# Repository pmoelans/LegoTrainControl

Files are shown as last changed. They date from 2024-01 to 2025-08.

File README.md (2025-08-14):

# Introduction
This project started out as a hobby project and got a tiny bit out of hand. The goal of the project was to create a custom controller for lego power functions trains. 
The specific goal was to get rid of the infrared controller and use Wifi instead. The Wifi turned out to be an issue since the connection time of the arduino boards with wifi can take a while and the attention span of 
kids is rather limited. Hence the current controller is now working with the ESPNOW protocol. 
Currently the project contains 3 seperate modules:
+ The train controller
+ The switch controller
+ The user controller(UI)
The following paragraphs describe the seperate modules.

## The train controller
The train controller is the hardware and software that is onboard the train itself and it controls the power functions motor. This module is build around the QTPY-C3 ESP32 platform. 
The form factor was the driving force behind the choice of platform. Namely the entire contraption (including battery) needs to have a similar size as the battery box of a powerfunctions motor. This puts some
serious constraints on the design. The platform also needs a few additional features with respect to the original power functions versions:
+ An emergency stop function: once this command is given, all trains need to stop as quickly as possible. This is a software thing and does not impact the overal design
+ An shutdown feature: once this command is given. The train stops and the entire circuit needs to be shut down. This has an impact on the hardware of the project in such a way that the ESP can shut itself down.
+ The basic idea for this controller was first found on https://mattzobricks.com/. A must see for Lego train enthousiasts. On this site there was a section where a similar controller as mine was created. This controller
  did not fit my exact needs since it was used together with the Rocrail platform. But it served as a firm basis for the controller described here.
 
 ### Hardware
 The board is build up around the following two modules:
 + QTPY-C3 ESP32
 + TB6612 Dual motor driver (TB6612FNG). Instead of just using the chip, I used the existing ready made breakout board
 + Custom build PCB(I'm not an electronics engineer so I'm sure that things could have been done better and more efficiently)
 + 3D printed casing in which you can snap in the PCB board as well as fit the lego power functions connectors. The shape of the box is heavily inspired on the original power functions box and the box on https://mattzobricks.com/.
  
## The swith controller
The switch controller is the hard and software that is used to control the switch. We use end switches in order to detect whether the switch is in its final position. This works a bit easer since each type of lego
switch has its own movement which might take a little more time to make the actual switch.

### Hardware
Main parts:
+ ATTiny85A
+ L9110 motor controller
+ Small lego engine
+ Two end switches
+ Custom PCB
+ 3D printed casing for the PCB.

## The user controller(UI)
This is the handheld controller that is used to control the trains(for now). We can control the switches as well, but the UI is specifically designed to quickly change between trains in question. You can have multple trains
that are connected to the controller. The only limit is the memory of the ESP32.

### Hardware
The design of the UI is pretty straight forward and contains of:
+ A rotary button:
  + Rotating the button speeds up or slows down the train
  + Pushing the rotary button switches to the next train that is registered.
+ Two buttons:
  + Emergency stop button: stops all trains
  + A shut down button: shuts down all trains
This controller is also build around the QTPY-C3 board. 
  
### Software
The software uses the ESPNOW protocol the communicate with all the trains. The controller has two functions:
+ Listens for new trains: Upon startup of a train (battery is on) it will start sending connection requests to the controller. This is done every few seconds until the controller sends an accept message to the train.
  After this accept request the train will send its status every 10s to the controller. The trains need to be identified and the unique identifier used is the mac-address of the ESP32.
  This mac-address together with the current state of the train(e.g. speed, battery voltage) are kept as well.
+ Controls the current train: Every time the rotary button is used, a message is send that reflects the changes. This message is only send to the train that is active at the moment. The state of the current train is also updated once the
    rotary button is used. Every new train creates a new entry in the dictionary
If one of the two other buttons is pressed, the message is send to all the trains.

# Future work

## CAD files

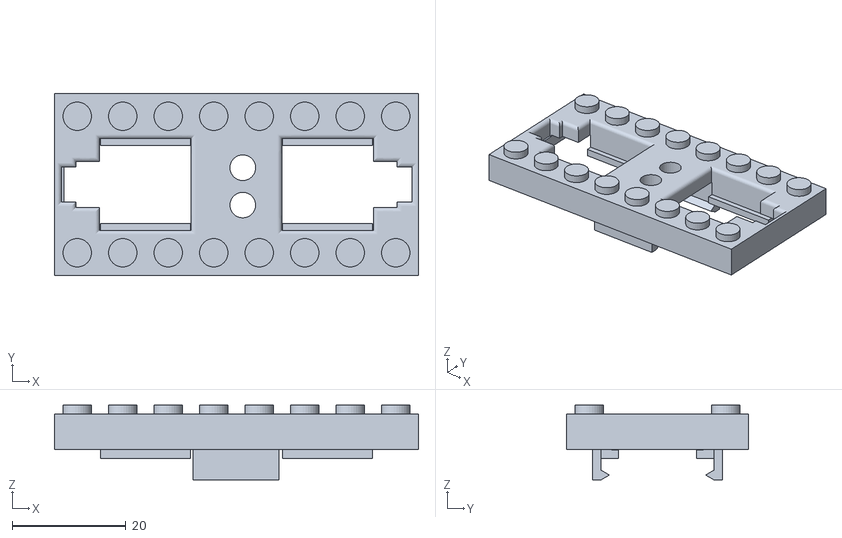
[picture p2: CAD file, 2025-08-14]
LegoEngineControlESPNow/Stl/TopSnap.stl
64.0 x 32.0 x 13.2

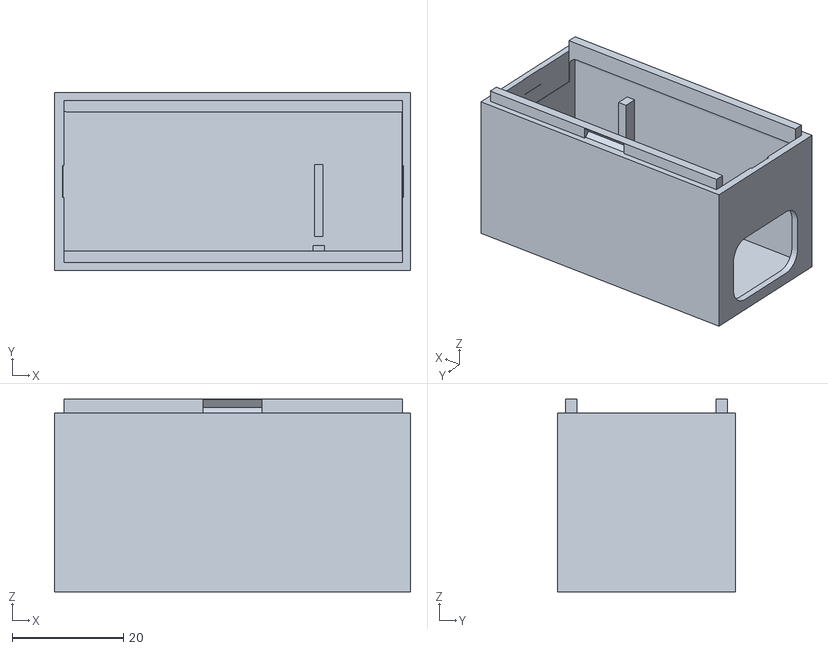
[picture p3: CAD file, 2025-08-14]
LegoEngineControlESPNow/Stl/Bottom.stl
64.0 x 32.0 x 34.7

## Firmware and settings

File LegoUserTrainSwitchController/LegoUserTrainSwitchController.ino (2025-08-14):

#include "RotaryBtn.h"
#include "Settings.h"
#include <esp_now.h>
#include <WiFi.h>
#include <esp_wifi.h>
#include <ArduinoJson.h>
#include "ClientHandler.h"
#include <Arduino_Helpers.h>
#include <AH/Hardware/Button.hpp>
#include <SoftwareSerial.h>
#include "enums.h"

#define DEBUG true // Set to false to disable debug prints
#if DEBUG
#define debug(x) Serial.print(x)
#define debugln(x) Serial.println(x)
#else
#define debug(x)
#define debugln(x)
#endif

int counter = 0;
int resendCount = 0;
int maxResendCount = 10;
int restartCount=0;
bool preState=1;
uint8_t ownMac[] = {0xC0, 0x4E, 0x30, 0x80, 0x72, 0x4C};

ClientHandler clientHandler;
SoftwareSerial mySerialLink(Rx, Tx);  //16 MOSI(RX) 14 MISO(TX)   

RotaryBtn SpeedBtn(5, 6, 1);
RotaryBtn SwitchBtn(7,8,11);

bool trainSelected = false;
bool reverseDirection = false;
long debounceDelta = 1000;
long pressTime =millis();

esp_now_peer_info_t peerInfo;
const int freq = 5000;//30000;
const int motorchannel1 = 0;
const int resolution = 8;
bool SwitchLights = false;


// callback function that will be executed when data is received
void OnDataRecv(const uint8_t* mac_addr, const uint8_t* incomingData, int len) {

  debug("Packet received from: ");
  String clientId =  PrintMac(mac_addr);

  Serial.print("clientId:");
  Serial.println(clientId);

  //deserialize the data:
  //=====================
  DynamicJsonDocument doc(256);
  deserializeJson(doc, incomingData);

  //Write the incoming message to the serial connection
  //===================================================
  //char* Mymessage= (char*) incomingData; 
  //mySerialLink.write(Mymessage);

  String clientType= doc["ClientType"];



  //check if we need to add the client:
  //===================================
  if (clientHandler.CheckClient(clientId, (uint8_t*)mac_addr,clientType)) {
    //register the peer device:
    //=========================
    //debug("Registering new client: ");
    //debugln((uint8_t*)mac_addr);
    memcpy(peerInfo.peer_addr, mac_addr, 6);
    peerInfo.channel = 0;
    peerInfo.encrypt = false;
    //Serial.println(peerInfo.peer_addr);
    // Add peer
    if (esp_now_add_peer(&peerInfo) != ESP_OK) {
      debugln("Failed to add peer");
      return;
    }
  }
  else
  {
    debug("I know this client already: ");
    debugln(clientId);
  }
}

void IncreaseSpeedCallBack()
{
  debugln("Increase Speed");
  clientHandler.clientList[clientHandler.CurrentTrainId].UpdateState(10);
  SendMessage(clientHandler.clientList[clientHandler.CurrentTrainId].Idx);
}
void DecreaseSpeedCallBack()
{
  debugln("Decrease Speed");
  clientHandler.clientList[clientHandler.CurrentTrainId].UpdateState(-10);
  SendMessage(clientHandler.clientList[clientHandler.CurrentTrainId].Idx);
}
void UpdateSwitchStateCallback()
{
  debugln("Engage Switch");
  clientHandler.clientList[clientHandler.CurrentSwitchId].UpdateState(1);
  SendMessage(clientHandler.clientList[clientHandler.CurrentSwitchId].Idx); 
}
void NextTrainClient()
{
  debugln("Fetch next train");
  //deactivate blinking on current train
  clientHandler.clientList[clientHandler.CurrentTrainId].DeactivateBlink();
  SendMessage(clientHandler.clientList[clientHandler.CurrentTrainId].Idx);
  clientHandler.GoToNextClient(1,"Train");
  clientHandler.clientList[clientHandler.CurrentTrainId].ActivateBlink();
  SendMessage(clientHandler.clientList[clientHandler.CurrentTrainId].Idx);
}
void NextSwitchClient()
{
  debugln("Fetch next switch");
  clientHandler.GoToNextClient(1,"Switch");
}
void PreviousSwitchClient()
{
  debugln("Fetch previous switch");
  clientHandler.GoToNextClient(-1,"Switch"); 
}
void setup() {

  if(DEBUG)
  {
    Serial.begin(115200);
  }

  InitButtons();

  //Set device as a Wi-Fi Station
  WiFi.mode(WIFI_STA);
  esp_wifi_set_mac(WIFI_IF_STA, ownMac);
  mySerialLink.begin(115200);
  //Init ESP-NOW && restart the esp if it does not work
  while ((esp_now_init() != ESP_OK) && (restartCount<maxRetryCountEspNowStart)) {
    debugln("Error initializing ESP-NOW");
    restartCount+=1;
    delay(100);
  }
  if(restartCount==maxRetryCountEspNowStart)
  {
    ESP.restart();
  }

  debugln("EspNow started");

  // Once ESPNow is successfully Init, we will register for recv CB to
  // get recv packer info
  esp_now_register_recv_cb(OnDataRecv);

  //Register the funtions:
  SpeedBtn.RegisterCallBack(Motion::Positive,IncreaseSpeedCallBack);
  SpeedBtn.RegisterCallBack(Motion::Negative, DecreaseSpeedCallBack);
  SpeedBtn.RegisterCallBack(Motion::BtnPress,NextTrainClient);

  SwitchBtn.RegisterCallBack(Motion::Positive, NextSwitchClient);
  SwitchBtn.RegisterCallBack(Motion::Negative, PreviousSwitchClient);
  SwitchBtn.RegisterCallBack(Motion::Negative, UpdateSwitchStateCallback);

  ledcSetup(motorchannel1,freq,resolution); 
  ledcAttachPin(Led,motorchannel1);
  ledcWrite(motorchannel1, 180);
}


void InitButtons() {
  pinMode(buttonEBreak, INPUT);
  pinMode(buttonShutDown, INPUT);
  pinMode(switchLights,INPUT);

  pinMode(nextTrainBtn,INPUT);
  pinMode(PowerHold, OUTPUT);

  //pinMode(Led,OUTPUT);
  digitalWrite(PowerHold,HIGH);

  //digitalWrite(Led,HIGH);
}
void Blink(int cnt) {

  //for (int i = 0; i < cnt; i++) {
  //  digitalWrite(Led, LOW);
  //  delay(50);
  //  digitalWrite(Led, HIGH);
  //  delay(50);
  //}
}

void CheckReverseBtn(Button btn) {
  if (btn.update() == Button::Falling) {
    clientHandler.clientList[clientHandler.CurrentTrainId].ReverseDirection();
    return;
  }
}
//Shut yourself down please:
void ShutDown()
{
  digitalWrite(PowerHold,LOW);
}
void CheckLightsBtn()
{
  if(digitalRead(switchLights)==HIGH)
  {
    SwitchLights=true;
    SendMessage(clientHandler.clientList[clientHandler.CurrentTrainId].Idx);
  }
}
void CheckShutDownStateBtn() 
{
  if (digitalRead(buttonShutDown) == HIGH) {
    //Go over all the clients and perform a shutDown
    for(int i=0;i<clientHandler.idx;i++)
    {
      clientHandler.clientList[i].EnableShutDown();
      SendMessage(i);     
    }   

    delay(100);
    ShutDown(); 
  }
}

void CheckEmergencyBrakeStateBtn() {
  if (digitalRead(buttonEBreak) == HIGH) {
     for(int i=0;i<clientHandler.idx;i++)
    {
      clientHandler.clientList[i].EnableEmergencyBrake();
      SendMessage(i);     
      clientHandler.clientList[clientHandler.CurrentTrainId].DisableEnableEmergencyBrake();
    }       
  }
}

void loop() {
  CheckShutDownStateBtn();
  CheckEmergencyBrakeStateBtn();
  //GetNextClient();
  
  SpeedBtn.CheckState();
  SwitchBtn.CheckState();  
}

void SendMessage(int index)
{
  debug(clientHandler.clientList[index].ClientId);
  PrintMac(clientHandler.clientList[index].MacAddress);
  String msg = clientHandler.clientList[index].CreateJson();
 
  char Msg[90];
  StaticJsonDocument<90> statusDoc;
  statusDoc["ClientId"] = clientHandler.clientList[index].ClientId;
  statusDoc["Power"] = clientHandler.clientList[index].State;
  statusDoc["ShutDown"] = clientHandler.clientList[index].ShutDown;
  statusDoc["eStop"] = clientHandler.clientList[index].EStop;
  statusDoc["EnableBlink"]=clientHandler.clientList[index].EnableBlinking;
  statusDoc["ChangeLights"]= SwitchLights;
  serializeJson(statusDoc, Msg);

  //reset the lights again:
  //======================
  SwitchLights = false;


  esp_err_t result = esp_now_send(clientHandler.clientList[index].MacAddress, (uint8_t*)&Msg, sizeof(Msg));
  //const uint8_t* myCString = (const uint8_t*)msg.c_str();
  debugln(Msg);
  //esp_err_t result = esp_now_send(clientHandler.clientList[index].MacAddress, Msg, sizeof(Msg));

  if (result == ESP_OK) {
    debugln("Sent with success");
    resendCount = 0;
  } else {

    debugln("Error sending the data");
    if (resendCount < maxResendCount) {
      resendCount += 1;
      SendMessage(index);
    }
  }
}

String PrintMac(const uint8_t* mac_addr) {
  char macStr[18];

  snprintf(macStr, sizeof(macStr), "%02x:%02x:%02x:%02x:%02x:%02x",
           mac_addr[0], mac_addr[1], mac_addr[2], mac_addr[3], mac_addr[4], mac_addr[5]);

  String macString = "";
  macString = macStr;
  return macString;
}

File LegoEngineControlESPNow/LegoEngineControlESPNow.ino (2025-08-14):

//Versions
//version 1.3: Uses the chip instead of the break-out board

//13/03/'25
//limit the power/traction when the battery voltage is dropping.
//also keep the registration going until we receive message from the transmitter

#include "secrets.h"
#include <ArduinoJson.h>
#include <esp_now.h>
#include <WiFi.h>
#include "QtPy.h"
#include "StatusLed.h"
#include "EngineControllerStep.h"
#include "BtnPress.h"

#define WaitTime 2000 //the time we wait before we engage the switch off button. Or trigger on a second button press

#define DEBUG true // Set to false to disable debug prints
#if DEBUG
#define debug(x) Serial.print(x)
#define debugln(x) Serial.println(x)
#else
#define debug(x)
#define debugln(x)
#endif

//need to fill this in with the mac address if the receiver
//==========================================================
esp_now_peer_info_t peerInfo;

double VbatLimit = 7.5; //the battery voltage at which we are going to limit the power
double VbatMax = 9;
double vbat = 9;
bool eStop;
bool shutDown;
bool shutDownRequested=false;
bool enableBlinking=false;
long millis_pre;
long deltaMilli = 500; //interval with which we are sending data to the controller
int errorFactorVBatPower = 40;

long millisrealTimePre = 0;
char*  ClientId;

//test
StatusLed statusLed(500,500,Led,5,100);
StatusLed trainLights(500,500,LightsOn,5,100);
EngineControllerStep Engine1(100,5,en12, en1A, en2A,engineOn);
EngineControllerStep Engine2(100,5,en34, en4A, en3A,engineOn);
BtnPress Btn1(Btn,1000);


// callback function that will be executed when data is received
void OnDataRecv(const uint8_t* mac_addr, const uint8_t *incomingData, int len) {
    
  //deserialize the data:
  //=====================
  DynamicJsonDocument doc(90);
  deserializeJson(doc, incomingData);
  
  eStop = doc["eStop"];
  shutDown = doc["ShutDown"];
  bool changeLights=doc["ChangeLights"];

  //Change the state of the lights. 
  //We don't want to keep it in memory
  //==================================
  if(changeLights)
  {
    trainLights.ToggleState();
  }

  Engine1.SetPower((int)doc["Power"]);
  Engine2.SetPower(-(int)doc["Power"]);

  //digitalWrite(engineOn, HIGH);
  //check if we are allow to blink:
  enableBlinking=doc["EnableBlink"];
  if(enableBlinking>0)
  {
    statusLed.StartFastBlink();
  }
  else
  {
    statusLed.StopBlink();
  }

  //Check if we need to perform an emergency brake
  EStop();

  //Update the power settings
  VbatUpdateEngineState();

  //only send data every 10s after registering
  deltaMilli=defaultUpdateFrequency;
  
}

void setup() 
{
 
  
  //keep the arduino powered on
  pinMode(shutDownPin, OUTPUT);
  digitalWrite(shutDownPin, HIGH);

  //Set the led state to indicate that the controller is live
  if(DEBUG)
  {
    Serial.begin(115200);
  }
 // Get the MAC address of the device
  String macAddress = WiFi.macAddress();

  // Convert the MAC address to a char*
  char macAddressChar[macAddress.length() + 1];
  macAddress.toCharArray(macAddressChar, macAddress.length() + 1);
  ClientId=macAddressChar;

  debug("ClientId:");
  debugln(ClientId);

  WiFi.mode(WIFI_STA);

  //Init ESP-NOW
  if (esp_now_init() != ESP_OK) {
    debugln("Error initializing ESP-NOW");
    return;
  }
  
  // Once ESPNow is successfully Init, we will register for recv CB to
  // get recv packer info
  esp_now_register_recv_cb(OnDataRecv); 
  
  // Register peer
  memcpy(peerInfo.peer_addr, broadcastAddress, 6);
  peerInfo.channel = 0;  
  peerInfo.encrypt = false;
  
  // Add peer        
  if (esp_now_add_peer(&peerInfo) != ESP_OK){
    debugln("Failed to add peer");
    return;
  }

  trainLights.On();
  millisrealTimePre = millis();
}

//send the status to the controller or register if it is the first time:
//=====================================================================
void SendStatus() {
  StaticJsonDocument<300> statusDoc;
  statusDoc["ClientId"] = ClientId;
  statusDoc["ClientType"]= "Train"; //define the type
  statusDoc["Power1"] = Engine1.GetCurrentPower();
  statusDoc["Vbat"] = MeasureVbat();

  char Message[80] = { 0 };
  serializeJson(statusDoc, Message);

  esp_err_t result = esp_now_send(broadcastAddress, (uint8_t *) &Message, sizeof(Message));
   
  if (result == ESP_OK) {
    debugln("Sent with success");   
   
  }
  else 
  {
    debugln("Error sending the data");
  }  
}
double MeasureVbat() {
  vbat = (analogReadMilliVolts(Vbat)*3)/1000;
  return vbat ;  //we need to find a proper bridge for the batterymonitor
  
}

void EStop() {
  if (eStop ==1) {
    // Serial.println("Estop");
    //currentPower = 0;
    debugln("EstopActive");
    Engine1.EStop();
    Engine2.EStop();
    eStop=0;
  }
}

void PowerDown() {
  if (shutDown ==1  ) {
    debugln("ShutDown");
    Engine1.PowerDown();
    Engine2.PowerDown();
    digitalWrite(shutDownPin, LOW);
    digitalWrite(Led, LOW);
    digitalWrite(LightsOn, LOW);

  }
}
void VbatUpdateEngineState()
{
  double vbatMeas = MeasureVbat();

  Engine1.Update();
  Engine2.Update();

  PowerDown();
}

void loop() 
{  
  //send the data to the controller
  //===============================
  if ((millis() - millis_pre) > deltaMilli) 
  {    
    SendStatus();   
    
    millis_pre = millis();
  }

  //Measure the battery voltage and update the power
  //================================================
  VbatUpdateEngineState(); 
   
  //Update the state of the led:
  statusLed.UpdateState();

  millisrealTimePre = millis();

  //detect the buttonpress
  if(millis()>WaitTime)
  {
    if(Btn1.LongPressDetected())
    {
      shutDown=true;
    }    
  }
}

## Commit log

2023-08-29 working arduino code
2024-01-19 Added control of switch
2024-05-06 Fixed bug when Serial is not connected
    [ClientHandler.cpp, LegoUserTrainSwitchController.ino]
2024-10-22 ATTiny
    The ATTiny implementation is partially working. Either a timing issue or some hardware that needs to be adjusted. The switch only does the switch after a few attempts
    [ClientHandler.cpp, LegoEngineControlESPNow.ino, LegoUserTrainSwitchController.ino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]
2024-11-08 Added a new button detection
    Borrowed the button press code from the train controller. This seems to work, maybe a bit too long of a button press. But works anyway.
2024-11-10 Refined the button detection.
    The controller is now also working with the L9110H
2024-11-13 Working version
    This version used a different compiler(board ) for the ATTiny13A. Board settings are in the ino file
2024-11-14 Detect button press
    Now the ATTiny reacts on a button that is connected to one of the inputs and not on a power cycle. At startup the switch goes to end switch1 which means that the train goes straight. This is a cleane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
2024-12-05 First version
    The switch hub can control up to 8 switches at once
2025-02-05 working on the breakout board
2025-08-14 The STL Files for the casing
    [Bottom.stl, TopSnap.stl]
